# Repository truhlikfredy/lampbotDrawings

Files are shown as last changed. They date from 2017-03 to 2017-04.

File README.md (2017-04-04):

# Lampbot drawings

These drawings were made to modify the original structure and create mounts for servos in such way that the lamp can be articulated in any axis.

The dimensions were based on Luxo L-1 lamp and HS-5765MH servos, any other lamps or servors might not be fit for these drawings.
 
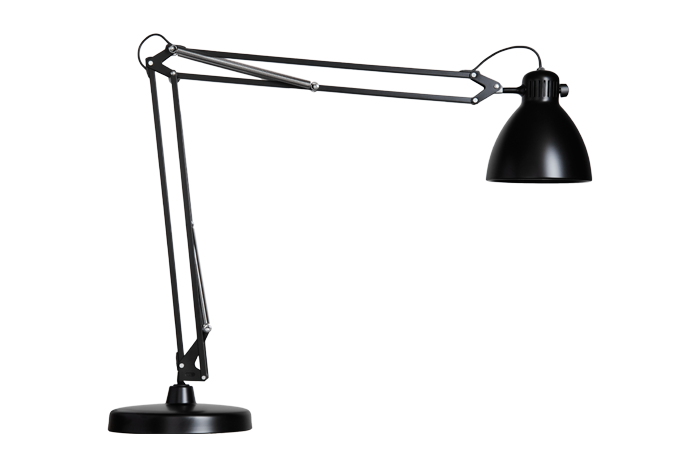
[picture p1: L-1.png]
lamp

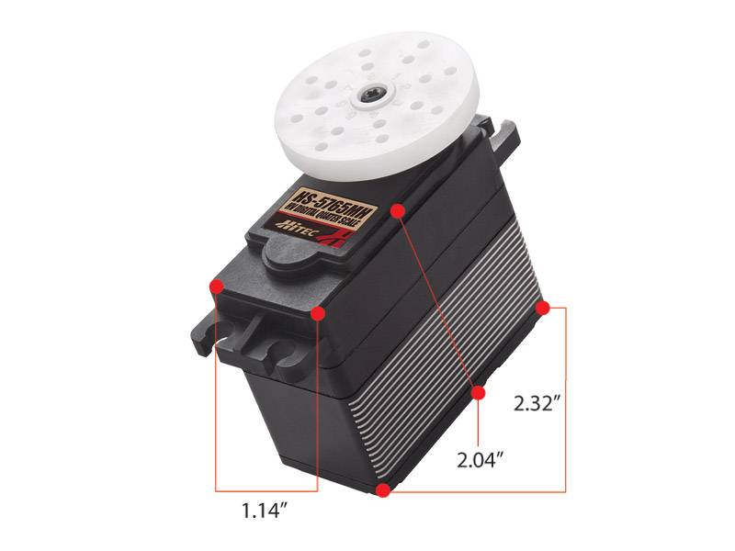
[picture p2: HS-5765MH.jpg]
servo


**Note:** Some adjustemnts were made to the parts to fit, that could be caused by my printer overextruding (if the filament diameter changed a bit and I didn't countered this change and just changed dimensions of the parts). It's possible that my drawings are not exact and inherit my workarounds around my printer. Printing these on proper comercial grade printer might not gurantee you perfect fit.

**Note 2:** I apologise if the drawings might look unclean, I'm just learning SolidWorks on short notice and I'm certain they could have be done much more efficiently, but for now this is best I can do :(

## Bottom Motor

Should hold servo motor to move around Z axis and is spaced in such way that the pivot of the servo will align with pivot of the lamp. The files are in SolidWorks and AutoCad as well, but I would recomend as for all others to use SolidWorks or STL (file format often used with 3D printers). The AutoCad was only exported as last backup for somebody who cares only about the footprint and has no access to anything else. But the real objects were designed in SolidWorks and printed from STL files.

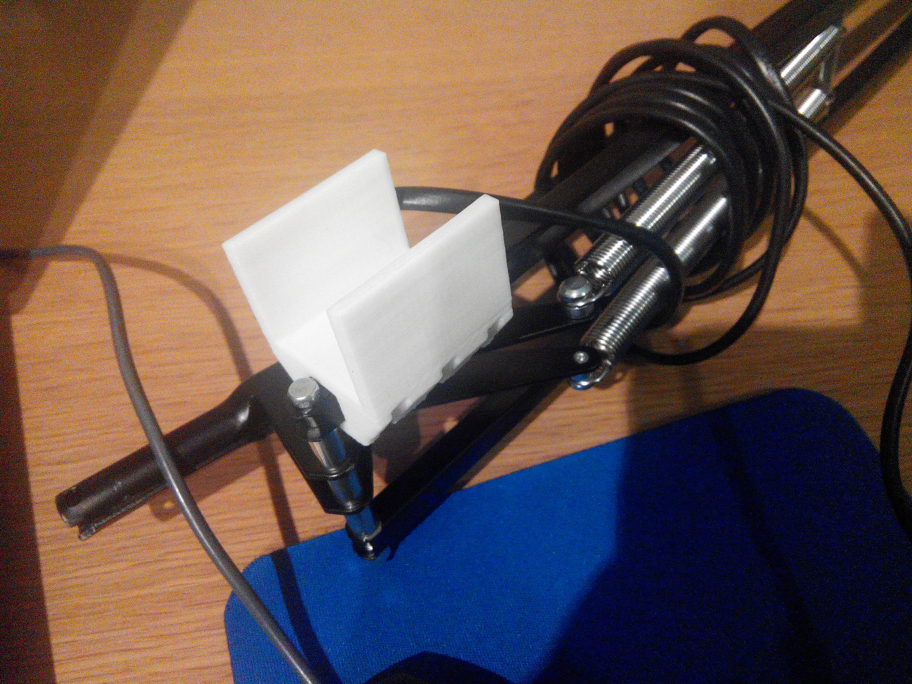
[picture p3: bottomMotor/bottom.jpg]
bottomPhoto

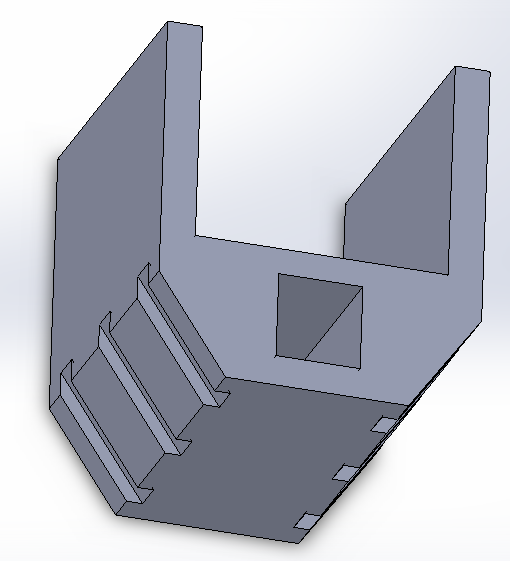
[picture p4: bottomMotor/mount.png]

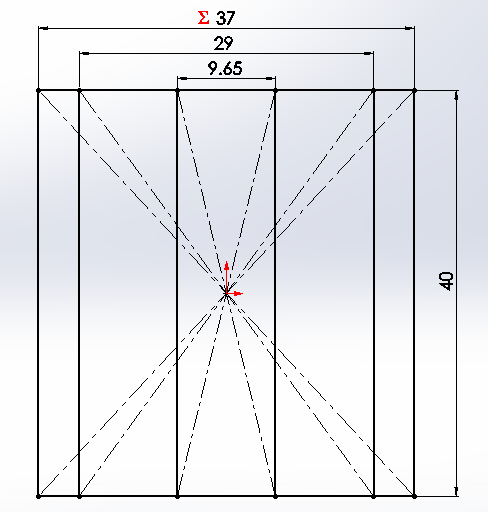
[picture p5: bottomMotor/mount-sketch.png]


I supply the florplan sketches as well just in case somebody wants to replicate these with wood, chisel and glue, some parts could be replicated by other means, not just 3D printing.

The bottom stripes are trenches for the zipties to get stuck in, so the will not slide around the mount.

Lamp Mount
--------
Just replacement for a nilon washer on the bottom of the lamp.

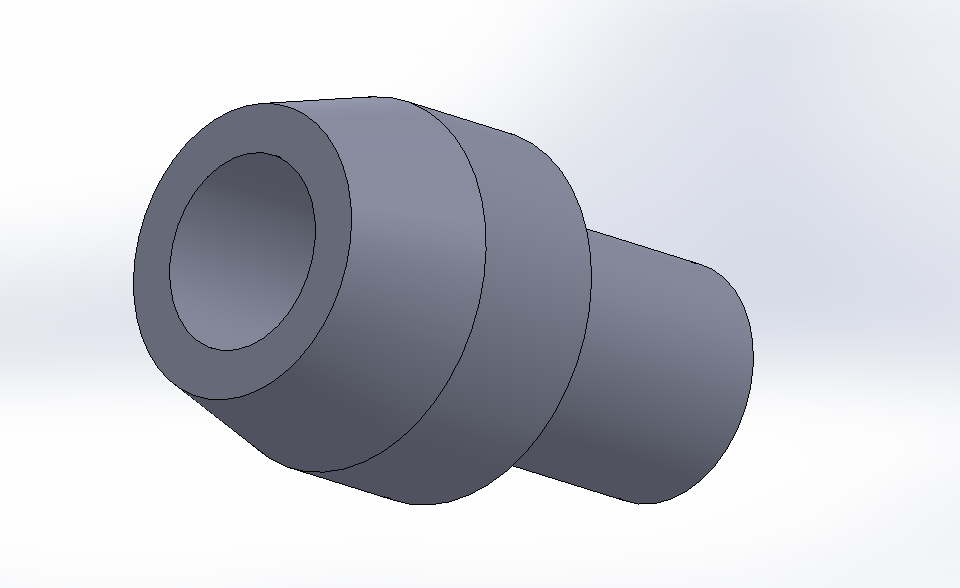
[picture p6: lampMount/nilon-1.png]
lampMount1

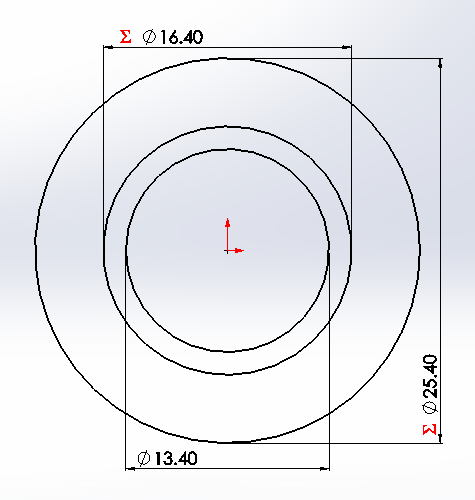
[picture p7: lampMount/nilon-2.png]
lampMount2


## Middle Bracket

Are the parts to move the elbow axis. First I was making only few experiments to replace the bracket with metal sheet and wanted to confirm the correct dimenstions of the V bracket.

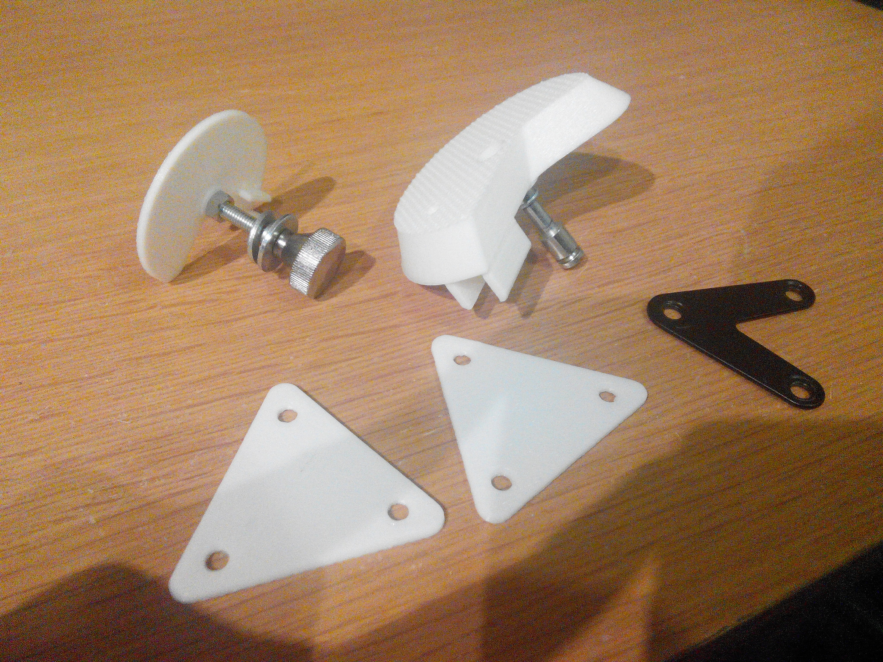
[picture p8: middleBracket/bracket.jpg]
elbow1


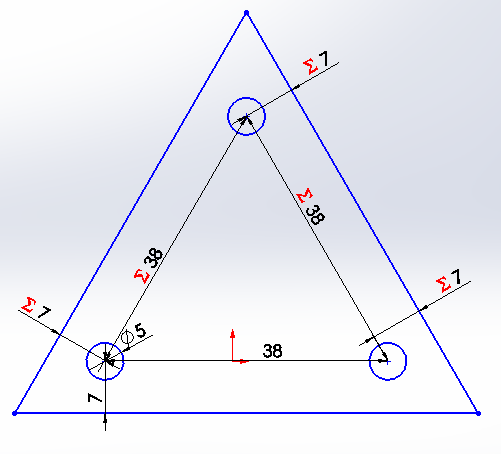
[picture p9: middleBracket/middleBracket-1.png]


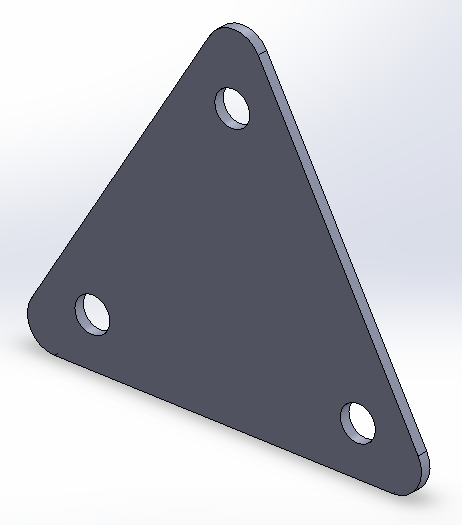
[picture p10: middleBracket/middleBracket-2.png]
elbowDimensions2


Then it evolved into holding mechanism as well, where I could articulate the arm as well. One aproach was to make a gear and drive it with stepper motor. But then I attempted a direct drive servo aproach. Where the holding V bracket would be turned into thick triangle, have support for the lamp and the servo at the same time.

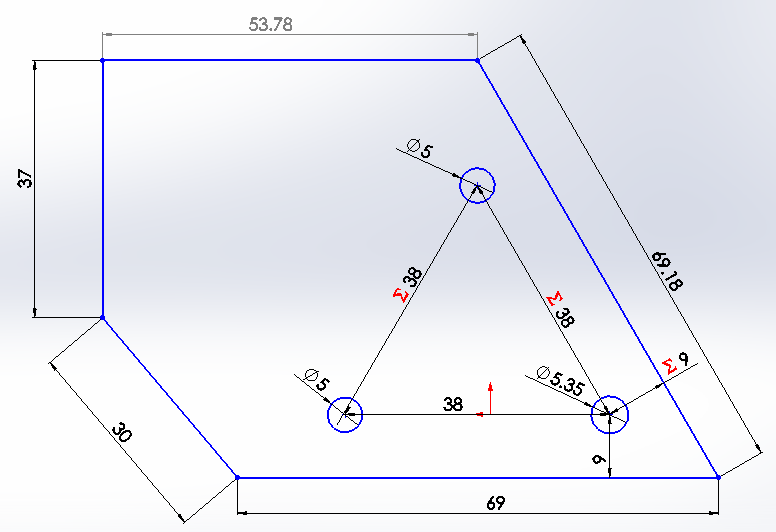
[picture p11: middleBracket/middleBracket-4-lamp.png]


Original V bracket was 1.5mm thick, if this has any chance to hold same absue while being made from PLA it had to be made much thicker. Because now the bracket is thicker the original shafts might not be long enough to support new thickeness. All except one were fine with the new change. Shaft in one hole had to be replaced with a new screw which is slighly wider than hole, this required increasing one hole by 0.35 mm. This is the reason why original bracket has 5mm holes and the thicker has one hole 5.35mm.

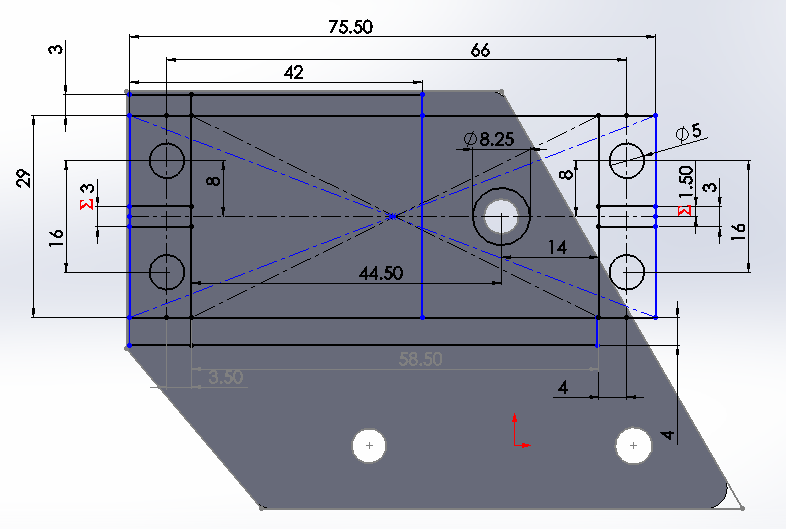
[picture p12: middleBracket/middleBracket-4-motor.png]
elbowMotorDimensions

The motor dimenstions were taken from datasheets, some from hand measurements and some just by trial / error to get the parts to fit just right.

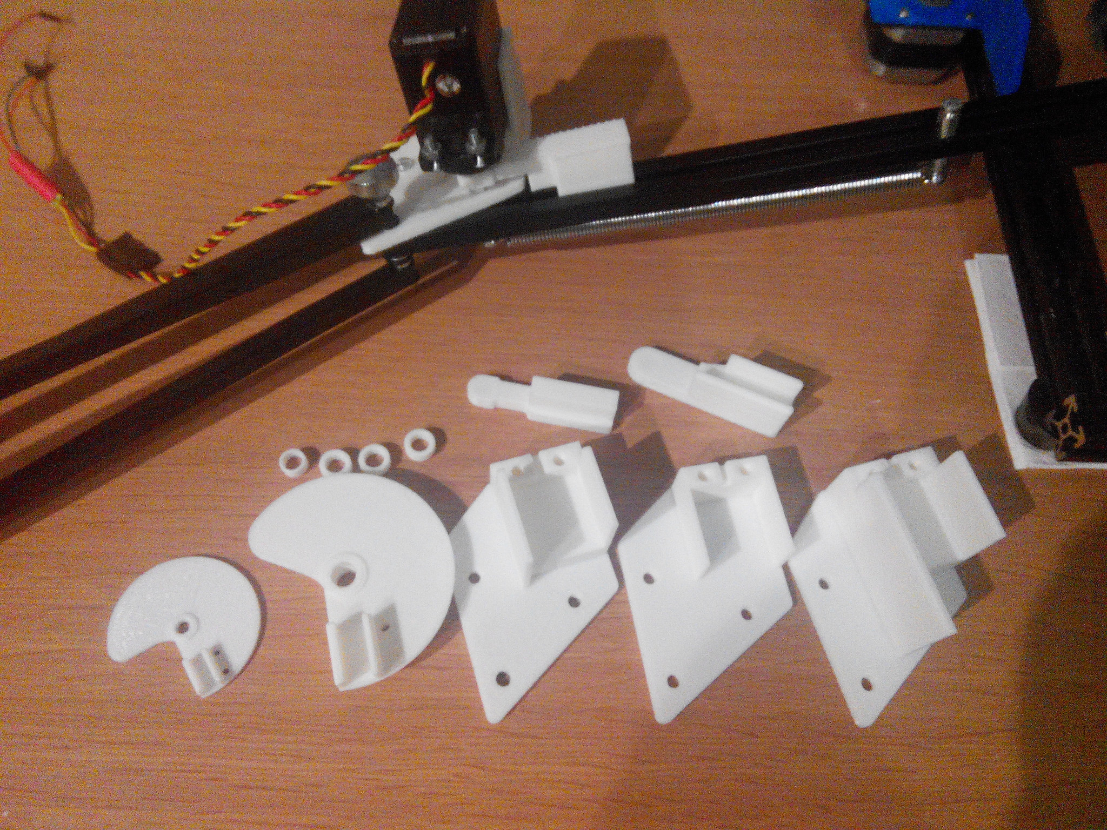
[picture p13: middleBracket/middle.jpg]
elbowIterations
 
Some parts took good few iterations to get it right.

### Elbow modified into bottom mount

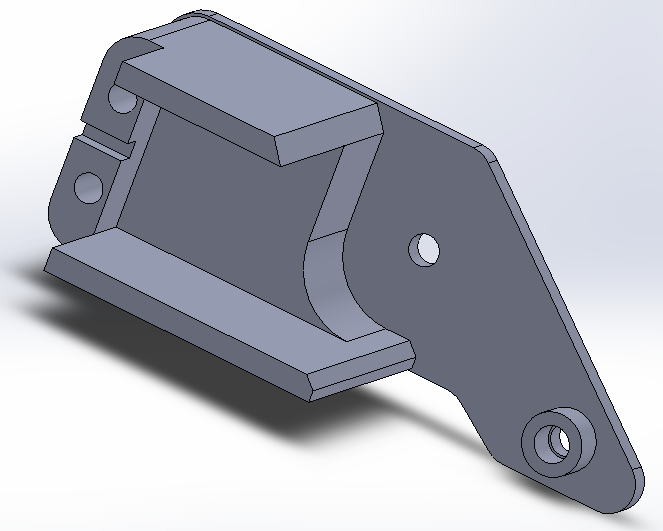
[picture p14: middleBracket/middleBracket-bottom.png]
bottom1


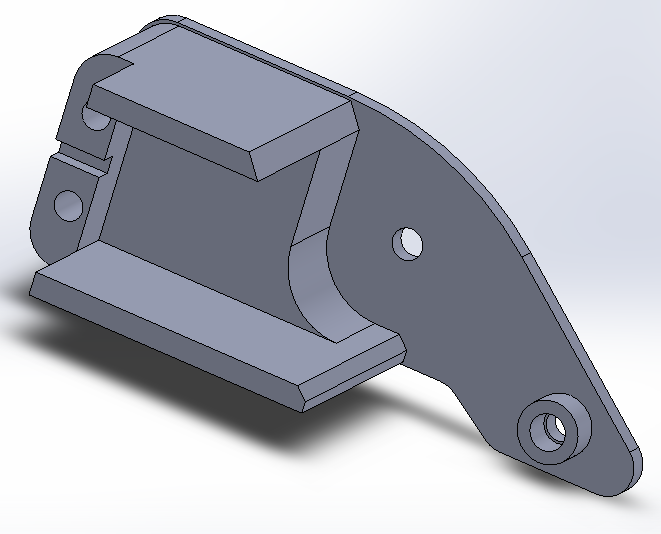
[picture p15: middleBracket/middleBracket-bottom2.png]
bottom2


This bottom mount requires longer servo arm **middleBracket/teeth3-long.SLDPRT**

### Servo arm

After getting servo mounted I needed to mount arm to it. The servo itself has small gear (15 teeth) which helps with a grip.

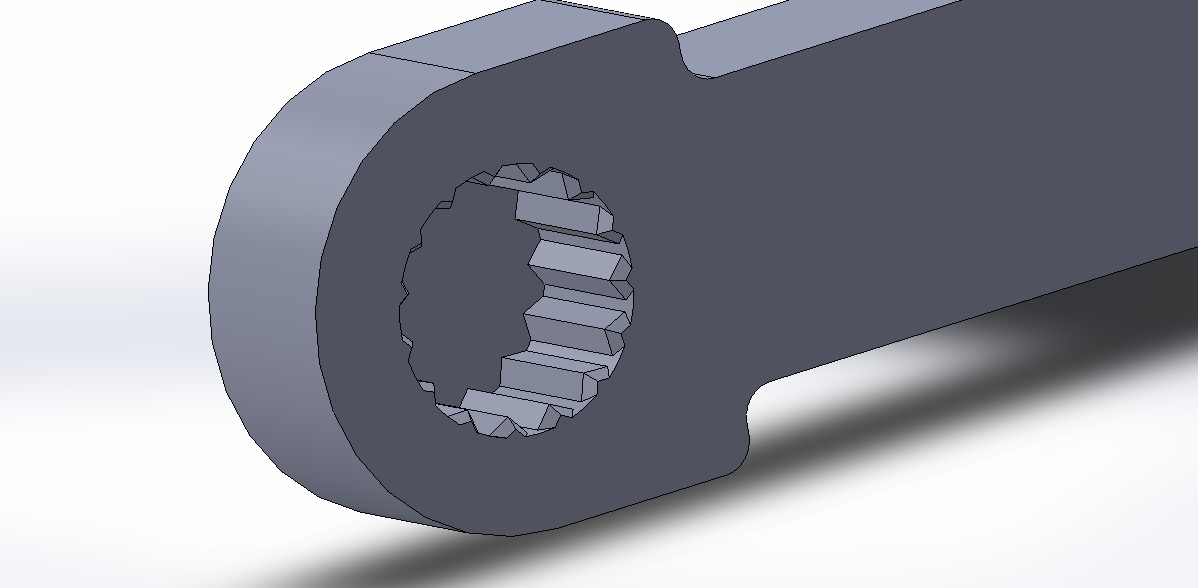
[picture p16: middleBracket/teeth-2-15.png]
teeth


On the end of the gear there is smal chamfer to ease the inserting of the arm.

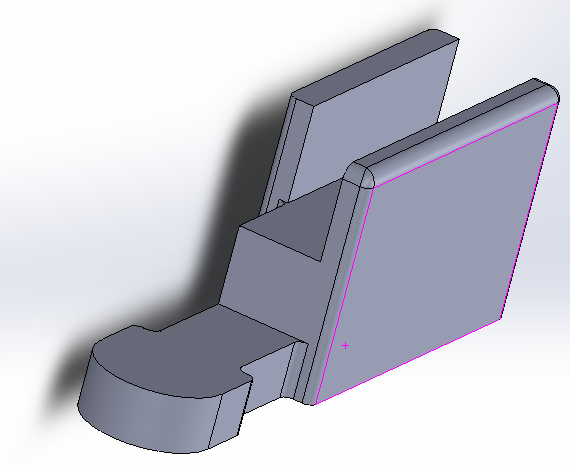
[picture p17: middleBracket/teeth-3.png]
teethRest


The rest of arm was made to snap around lamps arm, the different lenghts for supports are necesary to avoid colitions with other parts. Up movement is lest restrained, while in downwards movement are other things in the way so it needs to be shorter.

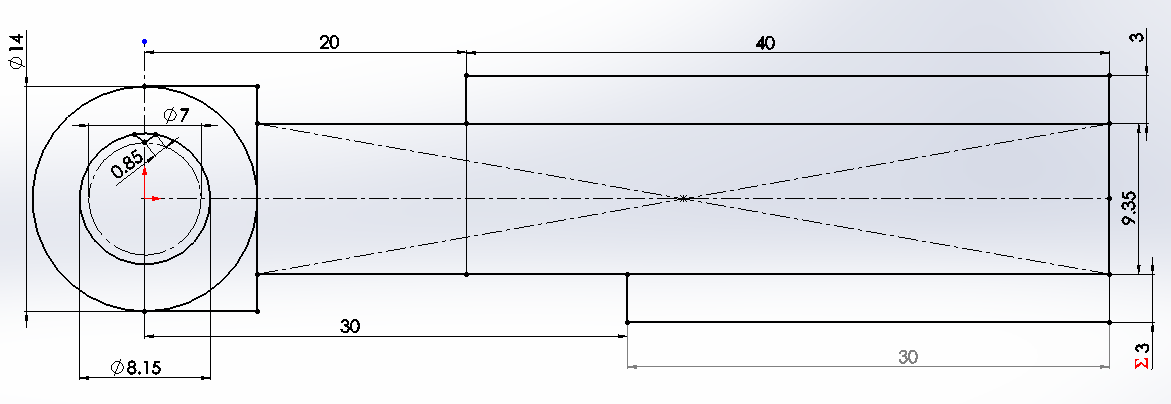
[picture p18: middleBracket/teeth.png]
teetDim


These are the dimensions, the teeth is desribed as triangle with one side 0.85mm long. Be very careful about this lenght. Because 0.05mm is difference between completely lose mount and mount soo tight that you will not able to fit it on. There is little margin for error to get it right and it took me multiple attempts. This might have to be tweaked for different printer because it's possible that I tweaked it around my current conditions instead of the true dimensions.

## Middle gear

This is unfineshed attempt to make half circle gear and drive this with stepper motor. The gears can be done easily in SolidWorks but I encountered other problems related to this aproach and at the moment this aproach is halted. 

But at least you can see how it evolved:

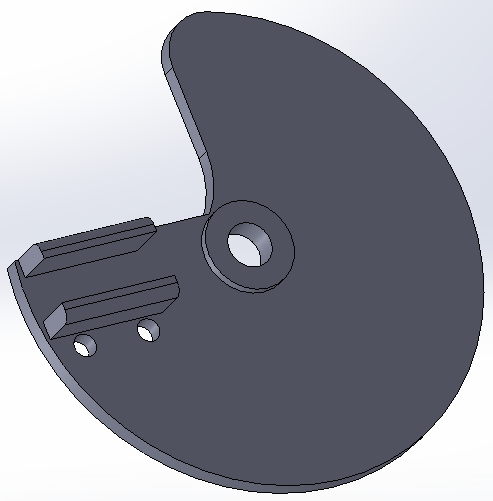
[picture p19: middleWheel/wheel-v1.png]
wheel


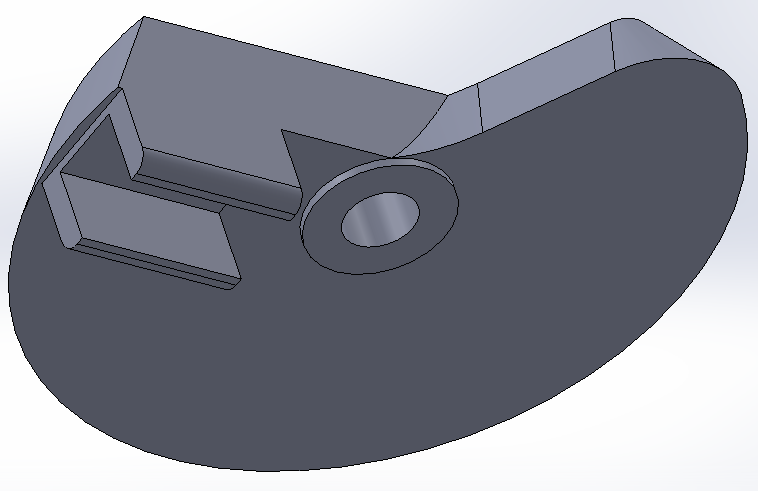
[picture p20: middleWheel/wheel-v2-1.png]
wheel


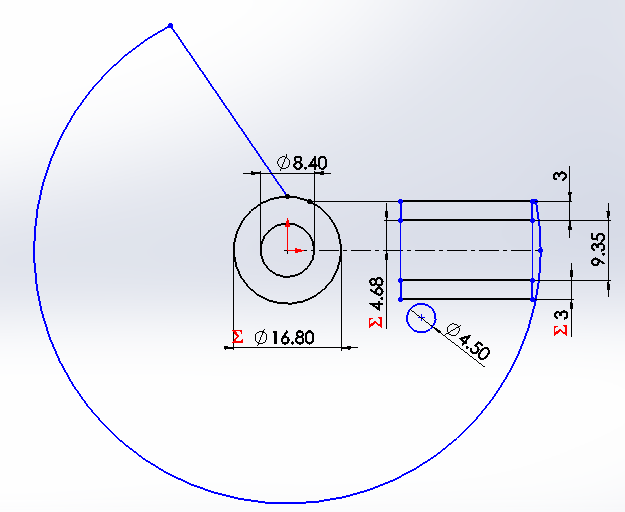
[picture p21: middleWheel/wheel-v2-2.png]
wheel


## Conclusion

Even only fraction of my experiments showed any promise, still it was worth the effort. The failed attempts might be fixed, the successful ones might be refined.

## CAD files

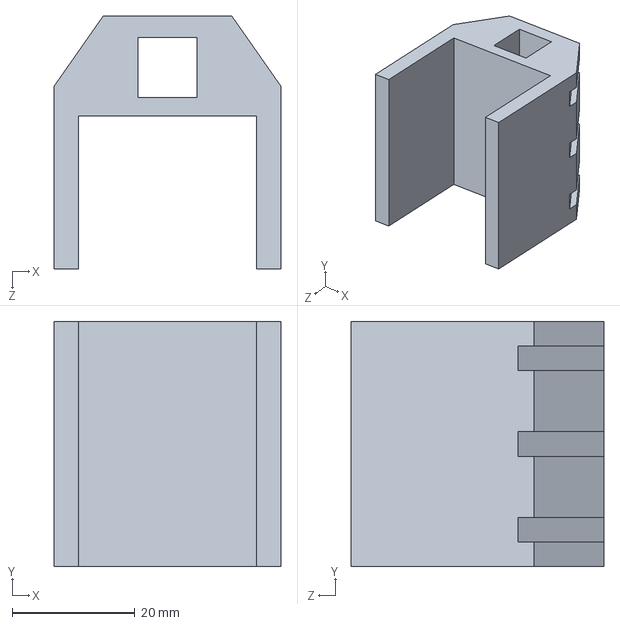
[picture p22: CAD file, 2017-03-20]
bottomMotor/servoMount.SLDPRT
37.0 x 40.0 x 41.3 mm

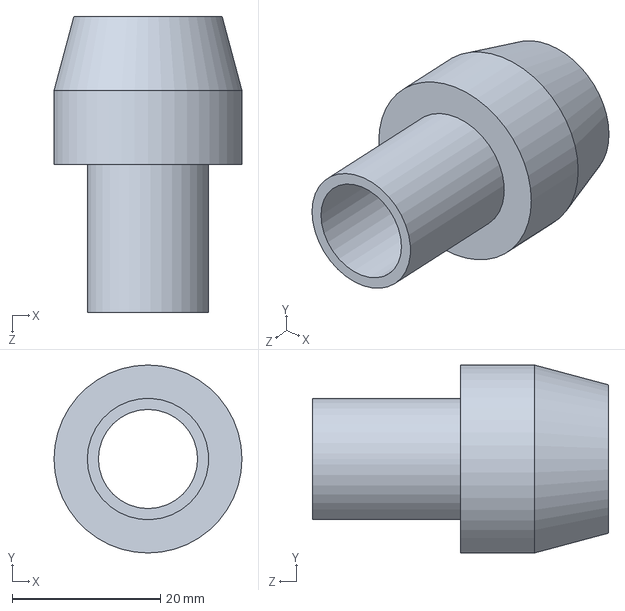
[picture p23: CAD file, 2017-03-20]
lampMount/nilonReplacement.SLDPRT
25.4 x 25.4 x 40.0 mm

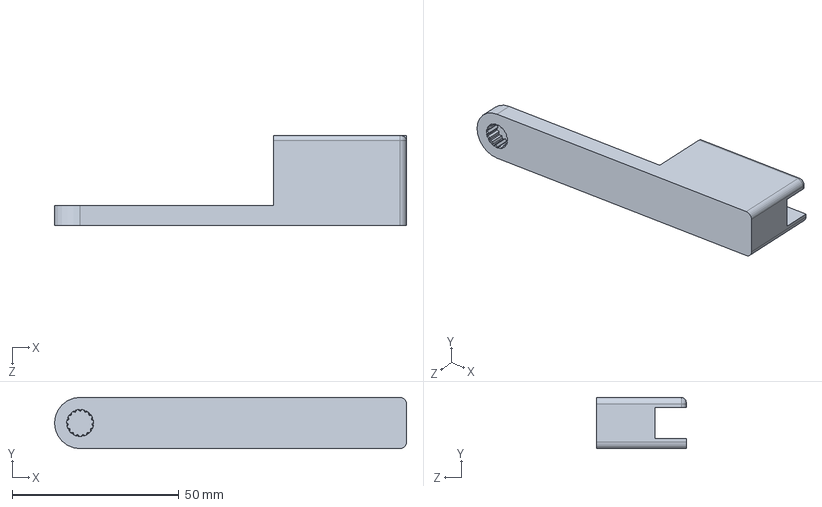
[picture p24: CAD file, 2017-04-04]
middleBracket/teeth3-long.SLDPRT
105.7 x 15.4 x 26.9 mm

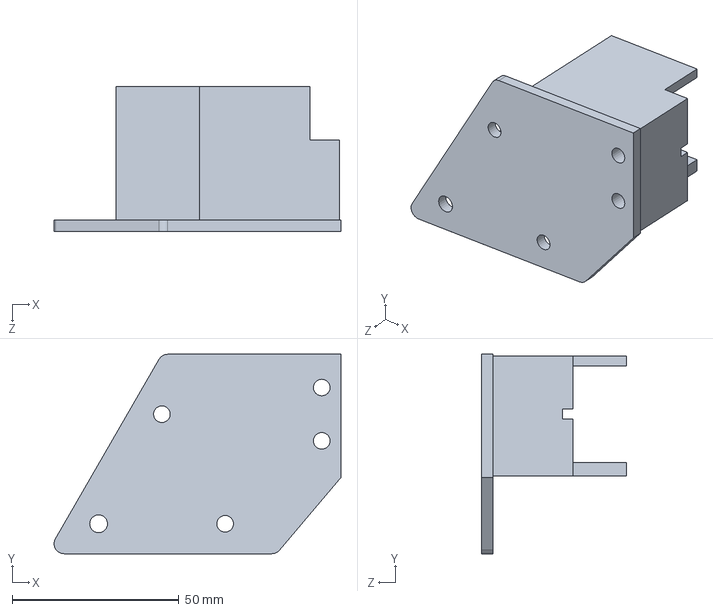
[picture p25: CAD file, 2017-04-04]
middleBracket/middleBracket4.SLDPRT
86.2 x 59.9 x 43.5 mm

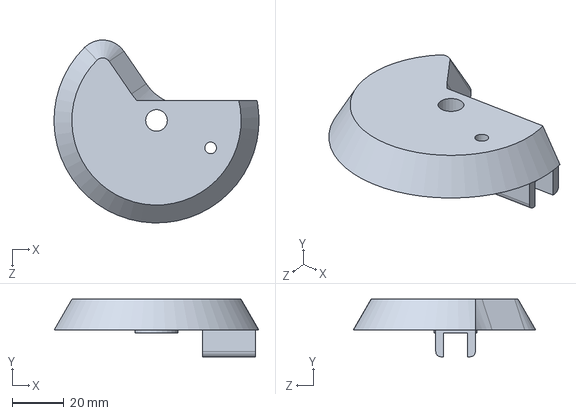
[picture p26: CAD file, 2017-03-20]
middleWheel/wheel-v2.SLDPRT
79.4 x 22.3 x 70.8 mm

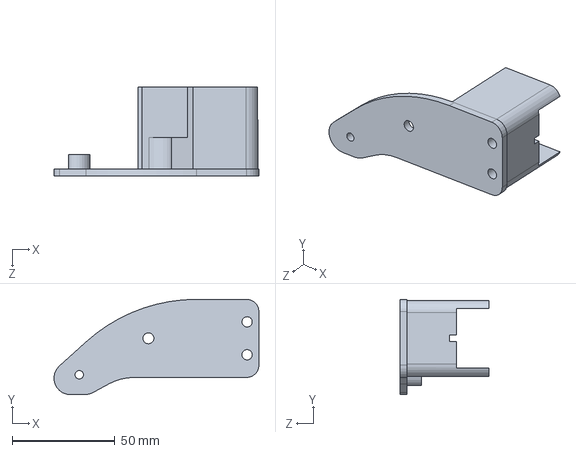
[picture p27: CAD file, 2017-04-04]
middleBracket/middleBracket4-bottom.SLDPRT
99.7 x 46.3 x 43.5 mm

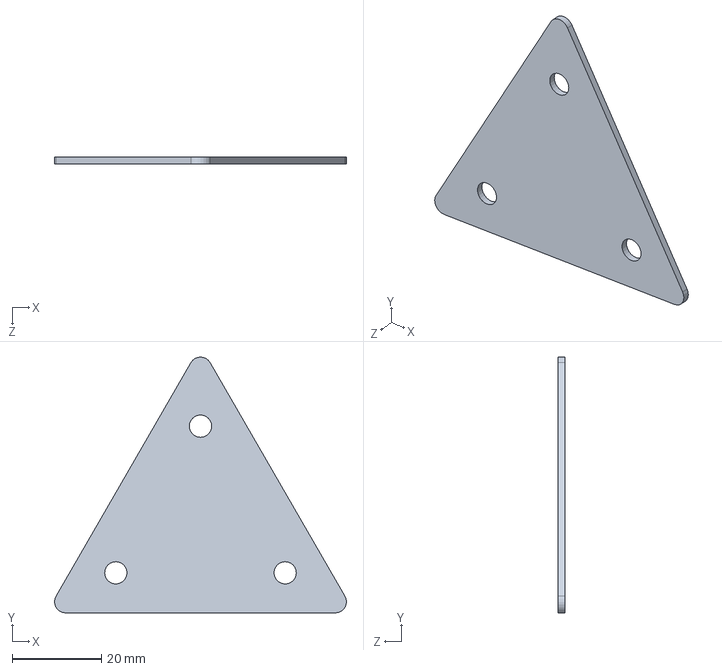
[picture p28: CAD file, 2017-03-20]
middleBracket/middleBracket.SLDPRT
65.5 x 57.4 x 1.50 mm

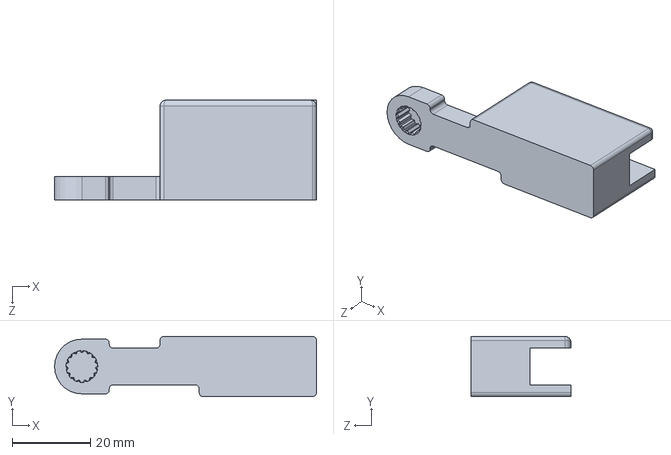
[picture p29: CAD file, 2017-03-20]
middleBracket/teeth2.SLDPRT
67.0 x 15.4 x 25.5 mm

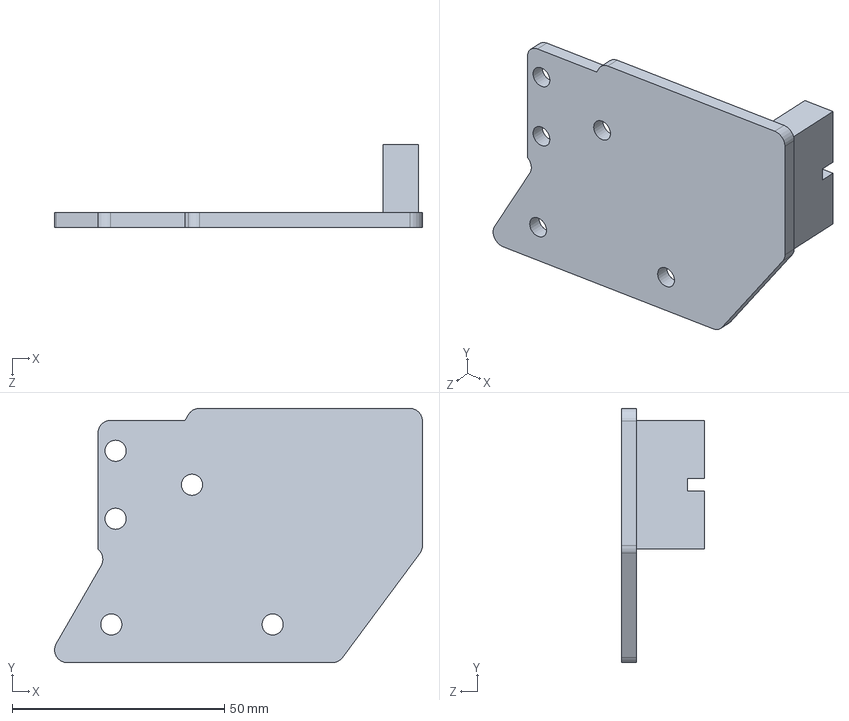
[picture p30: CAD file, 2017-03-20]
middleBracket/middleBracket2.SLDPRT
86.7 x 59.9 x 19.5 mm

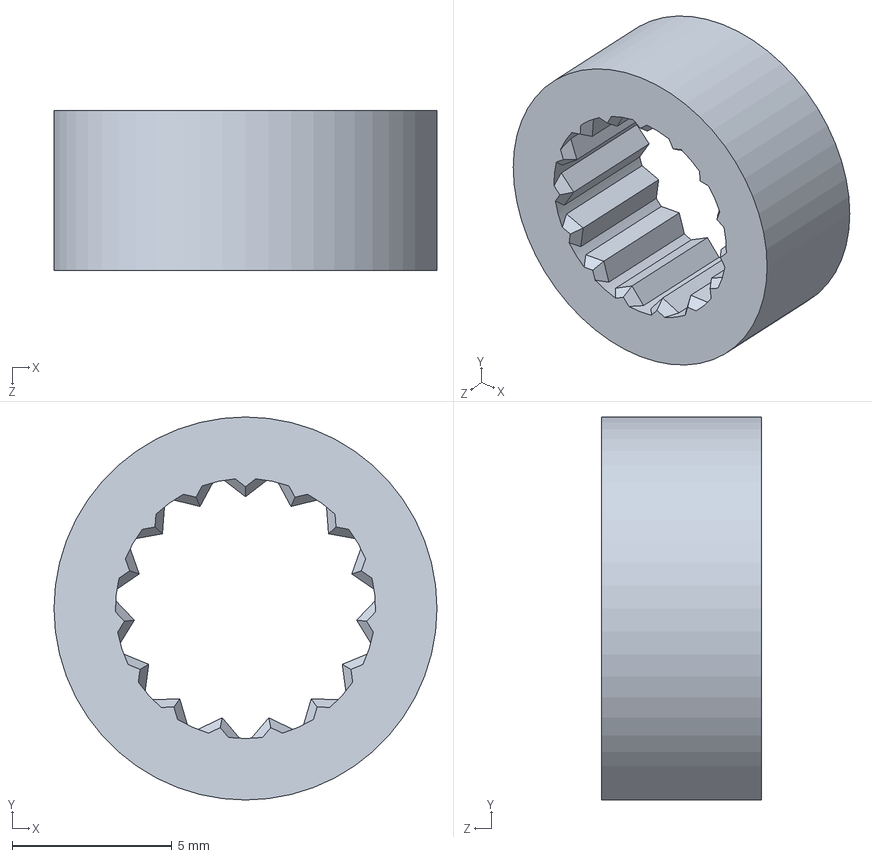
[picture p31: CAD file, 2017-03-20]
middleBracket/teeth1.SLDPRT
12.0 x 12.0 x 5.00 mm

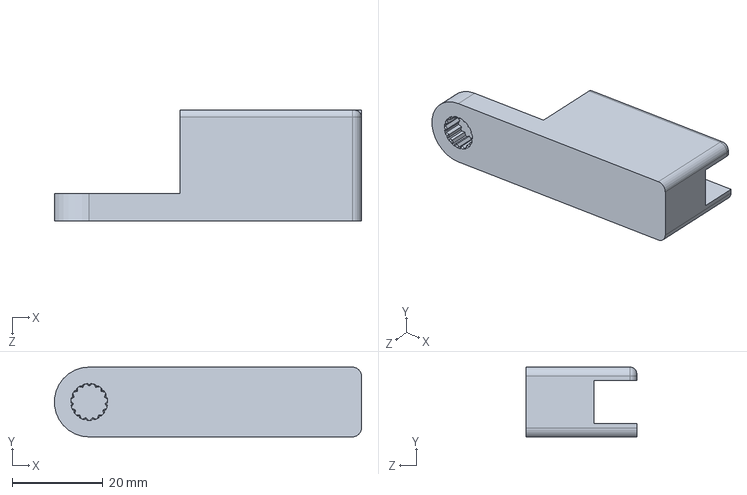
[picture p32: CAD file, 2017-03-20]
middleBracket/teeth3.SLDPRT
67.7 x 15.4 x 24.4 mm

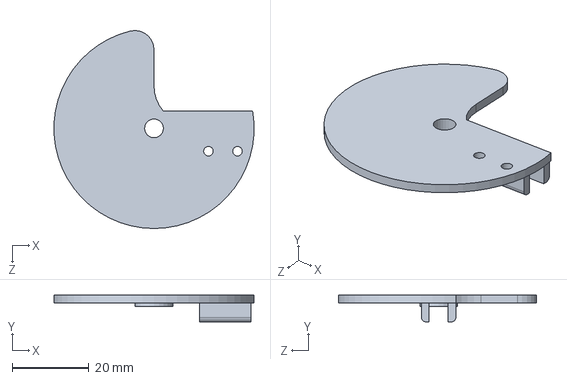
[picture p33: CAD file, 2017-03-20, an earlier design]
middleWheel/wheel-v1.SLDPRT
52.2 x 7.00 x 51.7 mm

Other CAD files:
middleBracket/middleBracket3.SLDPRT
bottomMotor/servoMount.DWG
bottomMotor/servoMount.STL
lampMount/nilonReplacement.DWG
lampMount/nilonReplacement.STL
middleBracket/middleBracket.DXF
middleBracket/middleBracket.STL
middleBracket/middleBracket3.STL
middleBracket/middleBracket4-bottom.STL
middleBracket/middleBracket4.DWG
middleBracket/middleBracket4.STL
middleBracket/teeth1.STL
middleBracket/teeth2.STL
middleBracket/teeth3-long.STL
middleBracket/teeth3.STL
middleWheel/wheel-v1.STL
middleWheel/wheel-v2.STL

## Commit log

2017-03-20 All the drawings
    [middleBracket.DXF, middleBracket.SLDPRT, middleBracket.STL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]
2017-04-04 Bottom mounts with longer arms
    [middleBracket4-bottom.SLDPRT, middleBracket4-bottom.STL, middleBracket4.SLDPRT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]
